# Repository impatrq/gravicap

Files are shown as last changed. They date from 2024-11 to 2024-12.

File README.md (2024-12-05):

<div align="center">

# Proyecto GraviCap

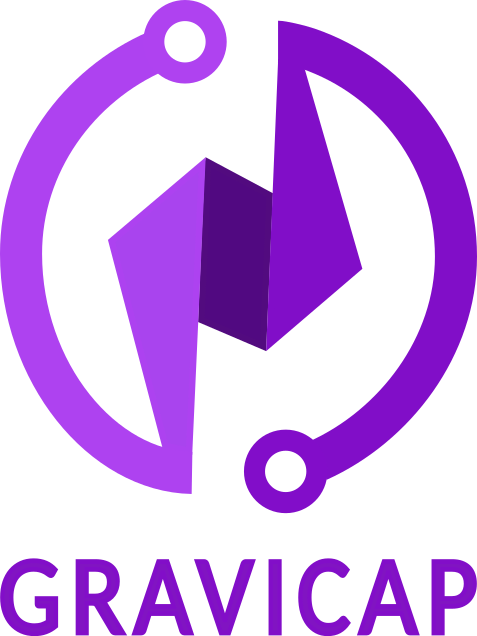
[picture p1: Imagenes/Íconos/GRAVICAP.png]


&nbsp;

| Página web | Email | Instagram | Linktree |
|---|---|---|---|
|[https://gravicap.vercel.app/home](https://gravicap.vercel.app/home)|gravicap.arg@gmail.com|[@gravi.cap](https://www.instagram.com/gravi.cap/)|[https://linktr.ee/gravicap](https://linktr.ee/gravicap)|

&nbsp;

</div>

## ¿Qué es GraviCap?
&nbsp;&nbsp;&nbsp;&nbsp;&nbsp;&nbsp;GraviCap consiste en un condensador de energía gravitatoria junto a un sistema de control de consumo.<br>
&nbsp;&nbsp;&nbsp;&nbsp;&nbsp;&nbsp;Un condensador de energía gravitatoria, o batería de gravedad es una estructura que eleva una carga consumiendo energía eléctrica, para luego almacenarla en forma de energía potencial gravitatoria. El sistema de control de consumo, revisa constantemente elconsumo de energía de la red, eligiendo el momento indicado para soltar la carga, que generará la energía cinética que, luego, será transformada en energía eléctrica por un generador.<br>

## Beneficios
&nbsp;&nbsp;&nbsp;&nbsp;&nbsp;&nbsp;GraviCap es un proyecto ideado para acompañar a los distintos generadores de energías renovables, adaptándose a las dimensiones que desee utilizar su consumidor acorde a la capacidad de su red eléctrica. Procura resguardar su huella de carbono al estar conformado por piezas simples sin requerimientos técnicos en demasía. Gracias a esto, pueden estar fabricadas por materiales reutilizados, derivados de materias primas locales o biomateriales. Permite prescindir aquellos materiales que perjudican al ambiente durante su producción o con su posterior desecho, ya que no hay materiales peligrosos para proteger.<br>
&nbsp;&nbsp;&nbsp;&nbsp;&nbsp;&nbsp;Almacenar energía gravitatoria nos permite ser también sustentables, ya que depende únicamente de un peso y la altura. El almacenamiento de energía es una problemática cada vez mayor, y con un planeta con crecientes problemas ambientales surgen problemas si estos son contaminantes.<br>

## Integrantes:
<div align="center">

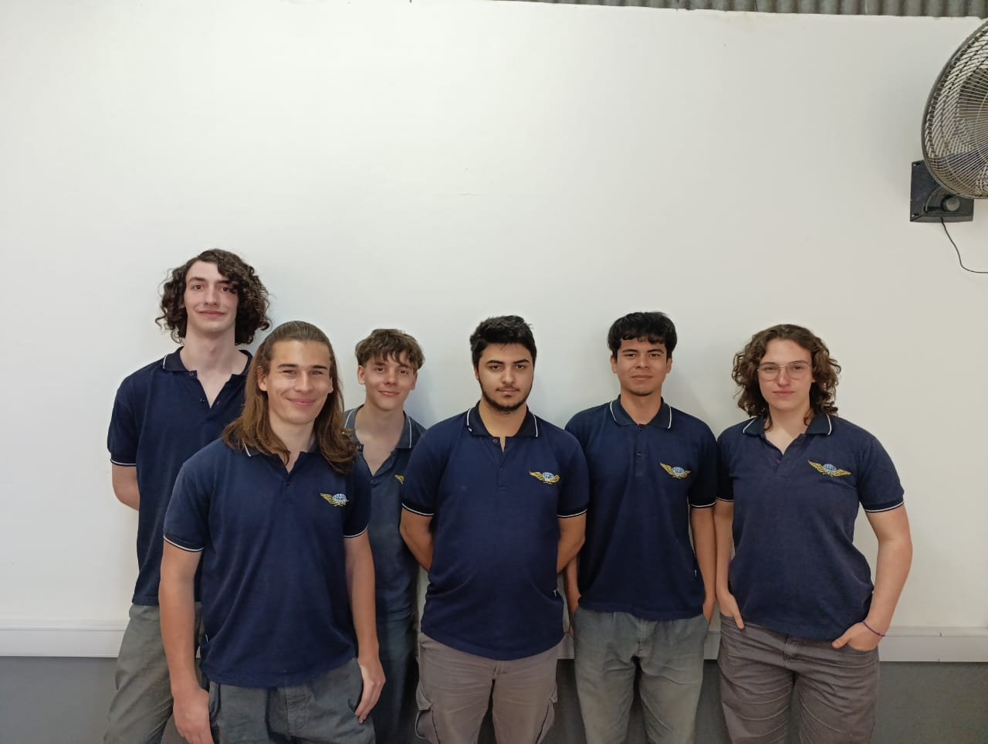
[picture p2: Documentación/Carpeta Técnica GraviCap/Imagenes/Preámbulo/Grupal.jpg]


</div>

### Fausto, Alvarez Mollo
Desarrollo de Electrónica y Documentación.

- 📷 Instagram: @fausto_73

- 📧 faustoalvarezmollo@gmail.com

- LinkedIn: [Fausto Alvarez Mollo](https://www.linkedin.com/in/fausto-alvarez-mollo/)

### Mariano Joaquín Bianqui Kronemberger
Desarrollo Web.

- 📷 Instagram: @marciano_moreno_piripiri

- 📧 marianobianqui@gmail.com

- LinkedIn: [Mariano Joaquín Bianqui Kronemberger](https://www.linkedin.com/in/mariano-bianqui-5035bb303//)

### Tomás Joaquín Calleja
Desarollo de Aplicación.

- 📷 Instagram: @tomii_calleja

- 📧 tomascalleja918@gmail.com

- LinkedIn: [Tomás Joaquín Calleja](https://www.linkedin.com/in/tomás-calleja-5a9894302/)

### Augusto Donatti
Desarrollo Estructural.

- 📷 Instagram: @donatti_augusto0211

- 📧 adonatti2005@gmail.com

- LinkedIn: [Augusto Donatti](https://www.linkedin.com/in/augusto-donatti-54a5bb303/)

### Tatiana Milena Felizia
Desarrollo de Software

- 📷 Instagram: @tati.felizia

- 📧 tatianafelizia@gmail.com

- LinkedIn: [Tatiana Felizia](https://www.linkedin.com/in/tatiana-felizia-9b29141bb/)

### Gabriel Jerónimo Takashi Sofía
Desarrollo de Marketing

- 📧 gabrielsofia19@gmail.com

- LinkedIn: [Gabriel Jerónimo Takashi Sofía](https://www.linkedin.com/in/gabriel-sofia-035335299/)

## Contactanos

### Instagram: [@gravi.cap](https://www.instagram.com/gravi.cap/)

### Pagina web: [gravicap.vercel.app](https://gravicap.vercel.app/home)

### Mail: gravicap.arg@gmail.com

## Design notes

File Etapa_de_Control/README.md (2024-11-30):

# Etapa de Control

&nbsp;&nbsp;&nbsp;&nbsp;&nbsp;&nbsp;La etapa de control es la encargada de sensar en __Tiempo Real__ distintos parámetros asociados al funcionamiento del sistema.
Una vez recolectados, los procesa para controlar el dispositivo y enviarlos a un [servidor web](https://github.com/impatrq/gravicap/tree/main/Servidor_Web).<br>
&nbsp;&nbsp;&nbsp;&nbsp;&nbsp;&nbsp;El sistema es ejecutado por un microcontrolador [RP2040-Zero](https://datasheets.raspberrypi.com/rp2040/rp2040-datasheet.pdf).<br>

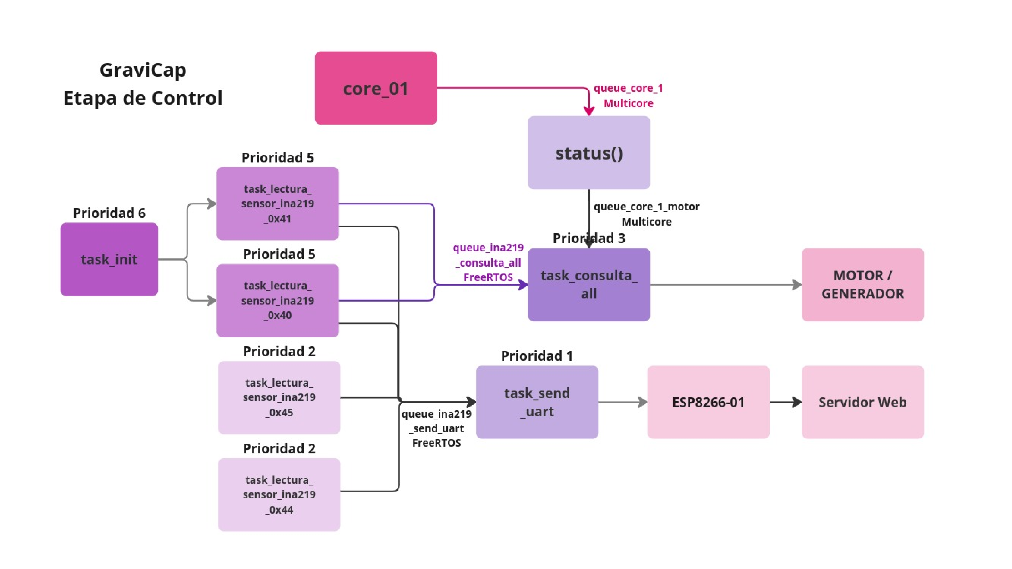
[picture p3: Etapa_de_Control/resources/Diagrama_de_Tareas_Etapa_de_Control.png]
Diagrama de Tareas de FreeRTOS

<div align="center">Diagrama de Tareas de FreeRTOS</div>

## Recursos utilizados
- [FreeRTOS](https://www.freertos.org/)
- [Pico-SDK](https://github.com/raspberrypi/pico-sdk/tree/master)
- [Multicore en RP2040](https://github.com/raspberrypi/pico-sdk/tree/master/src/rp2_common/pico_multicore) 
   
## Componentes utilizados
- [INA219](https://www.ti.com/lit/ds/symlink/ina219.pdf)  
- [Encoder Rotativo Incremental](https://en.wikipedia.org/wiki/Rotary_encoder)
- [ESP8266-01](https://www.espressif.com/sites/default/files/documentation/esp8266-technical_reference_en.pdf)

## Lenguaje utilizado  
&nbsp;&nbsp;&nbsp;&nbsp;&nbsp;&nbsp;C (con soporte de [PlatformIO](https://docs.platformio.org/en/latest/)).
    
## Tipos de comunicación serial  
- __UART__: En el intercambio de información con la [ESP8266-01](https://www.espressif.com/sites/default/files/documentation/esp8266-technical_reference_en.pdf).
- __I2C__: Usado para recibir la entrega de datos de los [INA219](https://www.ti.com/lit/ds/symlink/ina219.pdf), recibe datos en simultáneo desde 4 sensores.

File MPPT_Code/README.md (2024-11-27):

# MPPT - Maximun Power Point Tracking
&nbsp;&nbsp;&nbsp;&nbsp;&nbsp;&nbsp;El MPPT es una técnica utilizada en cargadores para obtener la máxima potencia posible cuando las condiciones de alimentación son inestables en el tiempo.<br>

&nbsp;&nbsp;&nbsp;&nbsp;&nbsp;&nbsp;Esta tecnología es aprovechada por una de las etapas del dispositivo, la que se asegura de convertir de forma óptima la energía entregada por el panel solar 
u otros generadores de energía utilizados. La etapa está conformada por un [circuito electrónico](https://github.com/impatrq/gravicap/tree/main/PCB/MPPT).<br>

&nbsp;&nbsp;&nbsp;&nbsp;&nbsp;&nbsp;El circuito incluye un microcontrolador [RP2040-Zero](https://datasheets.raspberrypi.com/rp2040/rp2040-datasheet.pdf), allí corre el programa presente en este directorio.<br>

## Recursos utilizados
- Lenguaje C (con soporte de [PlatformIO](https://docs.platformio.org/en/latest/))
- Comunicación serial I2C
- Converción Analógico Digital [ADC](https://github.com/raspberrypi/pico-sdk/tree/master/src/rp2_common/hardware_adc)
- [Pico-SDK](https://github.com/raspberrypi/pico-sdk/tree/master)

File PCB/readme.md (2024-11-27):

# PCB
&nbsp;&nbsp;&nbsp;&nbsp;&nbsp;&nbsp;Esta sección contiene todos los diseños de las placas utilizadas por GraviCap<br>

## Contenidos
- PCB Etapa de Control
- PCB MPPT
- PCB Placa de Conexión
  
&nbsp;&nbsp;&nbsp;&nbsp;&nbsp;&nbsp;Además, dentro de cada uno encontrarás:<br>
- Proyecto KiCad
- Archivo PCB
- Archivo SCH

## Recursos Utilizados
- [KiCad](https://www.kicad.org/)

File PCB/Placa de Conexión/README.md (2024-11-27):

Proyecto en KiCad del módulo Step-Down para una conexión a un celular.

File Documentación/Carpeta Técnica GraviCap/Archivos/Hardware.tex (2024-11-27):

\chapter{Hardware}
    
        \section{Introdución}
            El hardware de la Etapa de Control en el sistema \textcolor{dark_violet}{\textbf{GraviCap}} es crucial para la gestión precisa de la energía y el control del movimiento del peso. Esta etapa permite la correcta operación de los motores, sensores y actuadores, asegurando un funcionamiento eficiente del sistema de almacenamiento y conversión de energía. El diseño de este hardware se basa en la implementación de transistores y controladores que trabajan en conjunto para optimizar el flujo de energía y garantizar una operación estable.\par

        \section{Indicadores LED}
            \subsection{Introducción}
                El sistema de control de GraviCap incluye un conjunto de LEDs que proporcionan información visual sobre el estado del sistema y el nivel de carga de la batería. Los LEDs de la derecha indican el estado operativo del sistema, mientras que los LEDs de la izquierda muestran el porcentaje de carga de la batería. Los LEDs están dispuestos para facilitar el monitoreo y permitir una comprensión rápida del estado del sistema.\par
                
            \subsection{LEDs de la Derecha}
                Los LEDs ubicados a la derecha del sistema reflejan el estado general de operación:
                \begin{itemize} [label=•]
                    \setlength{\itemindent}{1.5em}
                    
                    \item Blanco: Indica que el sistema está encendido (ON).
                    \item Azul: Señala que el sistema está en modo de carga, es decir, la batería está recibiendo energía.
                    \item Rojo: Indica que el sistema está en modo de descarga, es decir, la energía almacenada en la batería está siendo utilizada.
                \end{itemize}
                Estos LEDs permiten monitorear el estado activo del sistema de forma clara, mostrando cuándo está operando, cargando o descargando energía.\par
                
            \subsection{LEDs de la Izquierda}
                Los LEDs de la izquierda muestran el porcentaje de carga de la batería, ordenados de arriba hacia abajo según el nivel de carga:\par
                \begin{itemize} [label=•]
                    \setlength{\itemindent}{1.5em}
                    
                    \item Azul: Indica que la batería está al máximo nivel de carga.
                    \item Verde: Señala que la batería está casi completamente cargada.
                    \item Verde (intermedio): Representa que la batería tiene un porcentaje de carga por encima de la mitad.
                    \item Amarillo: Indica que la batería está a la mitad de su capacidad.
                    \item Amarillo (inferior): Indica que la batería está en un nivel de carga inicial.
                    \item Rojo: Señala que la batería está en un estado de carga nulo, es decir, se ha descargado completamente o está cerca de agotarse.
                \end{itemize}
                
                 Este orden secuencial de los LEDs de la izquierda proporciona una visualización rápida del estado de carga de la batería, permitiendo a los usuarios evaluar en qué punto del ciclo de carga o descarga se encuentra la batería con solo un vistazo.\par

        \section{Sistema de Conmutación}
        
            \subsection{Introducción}
                El sistema de conmutación en la Etapa de Control de \textcolor{dark_violet}{\textbf{GraviCap}} se encarga de gestionar el encendido y apagado del motor que controla la masa gravitatoria. Para lograr esto de manera eficiente, se utilizan relés que permiten la conmutación del motor, y estos relés son controlados por transistores BJT. Este sistema garantiza que la conmutación de las corrientes de alto voltaje sea segura y precisa.\par
                
            \subsection{Funcionamiento del Sistema de Conmutación}
                El sistema de conmutación opera mediante un esquema de control en dos etapas. Primero, los transistores BJT actúan como interruptores que controlan la activación de los relés. Estos relés, a su vez, son responsables de conmutar las corrientes de mayor potencia necesarias para el funcionamiento del motor de elevación de la masa.\par
                \begin{itemize} [label=•]
                    \setlength{\itemindent}{1.5em}
                    
                    \item Conmutación con relés: Los relés se utilizan para abrir y cerrar los circuitos de alta corriente que alimentan al motor. Cuando se recibe una señal de control desde el microcontrolador, los BJT se activan, lo que a su vez energiza los relés y permite el paso de corriente hacia el motor.
                    \item Control preciso: El uso de transistores BJT para conmutar los relés permite que el microcontrolador tenga un control preciso sobre cuándo activar o desactivar el motor, asegurando que la operación de carga y descarga se realice en los momentos adecuados.
                \end{itemize}
                
            \subsection{Eficiencia del Sistema de Conmutación}
                El uso de relés para la conmutación del motor, en combinación con los BJT, proporciona un equilibrio entre eficiencia y seguridad. Los relés son ideales para manejar corrientes más altas, mientras que los BJT se encargan de conmutar las señales de control de baja potencia que provienen del microcontrolador.

                \begin{itemize} [label=•]
                    \setlength{\itemindent}{1.5em}
                    
                    \item Relés de alta capacidad: Los relés seleccionados para el sistema pueden manejar las corrientes y voltajes necesarios para operar el motor, asegurando una conmutación confiable sin generar excesivo calor o desgaste en el circuito.
                    \item Conmutación controlada por BJT: Los transistores BJT permiten que la conmutación de los relés sea precisa, ya que estos se activan con señales de baja potencia desde el microcontrolador, lo que garantiza un control eficiente sin necesidad de grandes corrientes para el accionamiento directo de los relés.
                \end{itemize}
                
            \subsection{Protección del Sistema de Conmutación}
                El sistema de conmutación incluye mecanismos de protección que garantizan la seguridad tanto de los relés como de los transistores BJT. Estos mecanismos aseguran que el sistema funcione de manera estable bajo diversas condiciones de carga.\par
                Se han implementado protecciones para evitar que corrientes excesivas dañen los relés o los transistores BJT. Estas protecciones son cruciales para prevenir fallos en el sistema, especialmente durante la conmutación de grandes cargas.\par
            
        \section{Resultado Final}
            \begin{figure}[H]
                    \centering
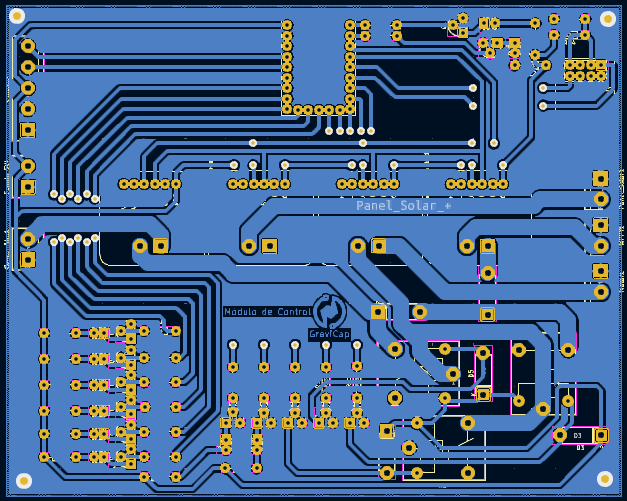
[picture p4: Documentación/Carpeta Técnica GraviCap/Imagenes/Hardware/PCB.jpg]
                    
                    \caption{PCB del Sistema de Control}
                    \label{fig:h1}
                \end{figure}

            \begin{figure}
                \centering
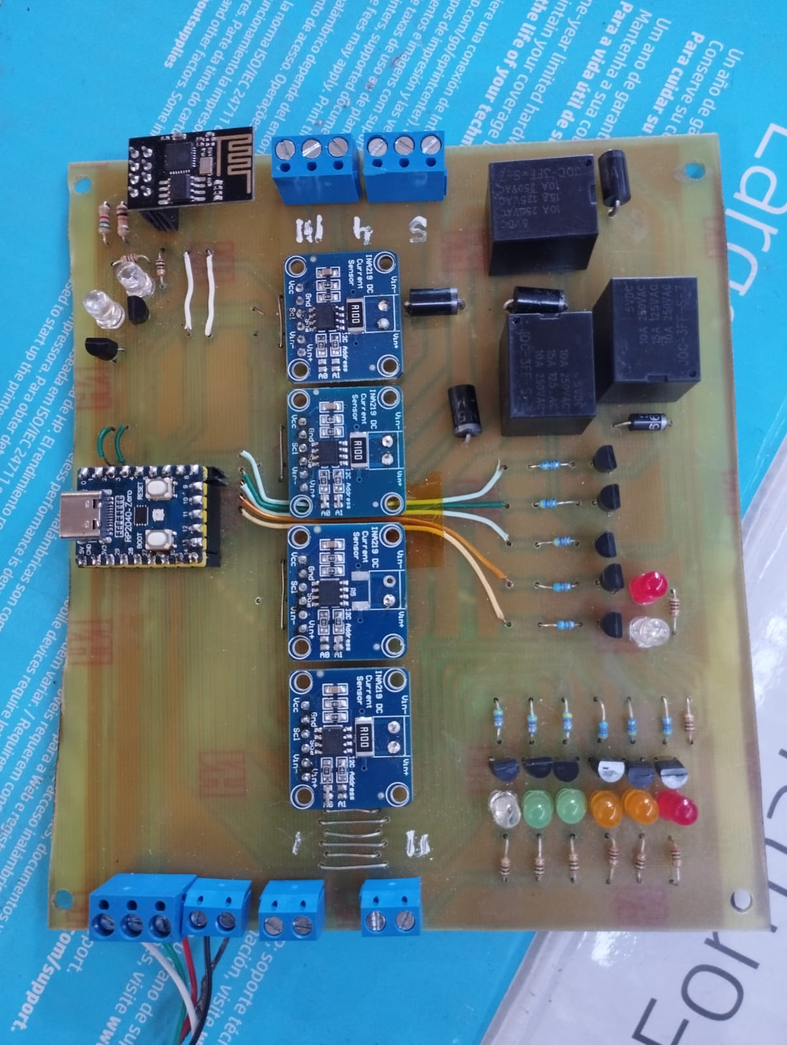
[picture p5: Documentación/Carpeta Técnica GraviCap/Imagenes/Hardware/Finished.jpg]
                
                \caption{PCB finalizado del Sistema de Control}
                \label{fig:h2}
            \end{figure}

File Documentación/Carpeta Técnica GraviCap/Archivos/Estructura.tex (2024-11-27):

\chapter{Estructura}

    \section{Introducción}
    
        Nuestra estructura está diseñada para aprovechar eficientemente la energía potencial gravitatoria mediante un sistema innovador que convierte dicha energía en electricidad utilizable para el consumidor. Este sistema, que se fundamenta en principios físicos sólidos, se basa en la capacidad de almacenar energía cuando se eleva un peso y liberarla controladamente al permitir que dicho peso descienda. Este proceso de elevación y descenso es crucial, ya que permite la conversión de la energía potencial gravitatoria en energía mecánica. A su vez, esta energía mecánica es transformada en energía eléctrica a través de un generador, completando así el ciclo de conversión.\par
        El concepto de energía potencial gravitatoria se basa en la relación entre la masa del objeto, la altura desde la cual se eleva y la fuerza de gravedad que actúa sobre él. Cuando un peso es elevado, se almacena una cantidad significativa de energía, que puede ser aprovechada posteriormente al liberar el peso y dejar que caiga. Este método de almacenamiento y liberación de energía es no solo eficiente, sino también innovador, ya que utiliza la gravedad, una de las fuerzas fundamentales de la naturaleza, como medio para generar electricidad.\par
        El sistema se configura de tal manera que maximiza la conversión de energía y minimiza las pérdidas durante los procesos de elevación y descenso. Al actuar sobre la energía potencial almacenada en el peso, se logra transformar dicha energía en un flujo eléctrico útil que puede ser utilizado para satisfacer las demandas energéticas de los consumidores. Este proceso, que involucra la mecánica del movimiento y la generación eléctrica, es clave para el funcionamiento de la estructura y para alcanzar los objetivos de sostenibilidad y eficiencia energética que perseguimos.\par
        A través de la implementación de este sistema, buscamos demostrar la viabilidad de las baterías gravitatorias como una alternativa renovable y accesible a otras formas de almacenamiento de energía, contribuyendo así a la transición hacia un futuro más sostenible y respetuoso con el medio ambiente.\par
        
    \section{Fundamentos de la Energía Potencial Gravitatoria}
    
        La energía potencial gravitatoria ($E_p$) es la energía que un objeto posee debido a su posición en un campo gravitatorio. En el caso de una batería gravitatoria, el objetivo es aprovechar esta energía elevando una masa a una cierta altura para luego, cuando la masa desciende, convertir esa energía en energía mecánica, y finalmente en energía eléctrica. La fórmula para calcular la energía potencial gravitatoria es:\par
        
        \begin{equation}
            E_p = mgh
        \end{equation}
        
        Donde:\par
        
        \begin{itemize} [label=•]
            \setlength{\itemindent}{1.5em}
            
            \item $E_p$ es la energía potencial en Joules [$J$].
            \item $m$ es la masa del objeto en kilogramos [$kg$].
            \item $g$ es la aceleración de la gravedad ($9,81 \nicefrac{m}{s^2}$).
            \item $h$ es la altura en metros [$m$].
        \end{itemize}
        
        La energía potencial gravitatoria es directamente proporcional a la masa ($m$) y a la altura ($h$). A mayor masa o mayor altura, se almacena más energía. En este sistema, el peso de 27 kg se eleva hasta una altura de 2,2 metros, por lo que la energía potencial almacenada es:\par

        \begin{equation}
            E_p = 27kg \times 9,81 \nicefrac{m}{s^2} \times 2,2m = 582,69 J
        \end{equation}
        
        Esto significa que, cuando el peso está en su posición más alta, el sistema puede almacenar 582.69 Joules de energía, la cual se puede liberar cuando el peso desciende. Si se aumenta la altura o la masa, la energía potencial se incrementará de manera proporcional.\par
        Para un sistema más complejo, donde se utilizan varias masas a distintas alturas, la energía potencial total del sistema sería la suma de las energías potenciales de cada una de esas masas. Esto se expresa como:\par
        
        \begin{equation}
            E_{Total} = \sum_{i=1}^{n} m_igh_i
        \end{equation}

        Dónde:\par

        \begin{itemize} [label=•]
            \setlength{\itemindent}{1.5em}
            
            \item $n$ es el número total de masas.
            \item $m_i$ es la masa de cada bloque.
            \item $h_i$ es la altura de cada bloque.
        \end{itemize}

    \section{Conversión de Energía Potencia a Energía Cinética}

        Cuando la masa desciende desde su posición elevada, la energía potencial gravitatoria ($E_p$) se convierte en energía cinética ($E_k$), que es la energía que un objeto tiene debido a su movimiento. La fórmula para calcular la energía cinética es:

        \begin{equation}
            E_k = \frac{1}{2} m v^2
        \end{equation}

        Dónde:
        \begin{itemize} [label=•]
            \setlength{\itemindent}{1.5em}
            
            \item $E_k$ es la energía cinética generada en Joules [$J$].
            \item $m$ es la masa del objeto en kilogramos [$kg$].
            \item $v$ es la velocidad del objeto en metros sobre segundo [$\nicefrac{m}{s}$].
        \end{itemize}

        Durante el descenso, la masa comienza a ganar velocidad a medida que pierde altura. En un sistema ideal sin pérdidas por fricción o resistencia del aire, la energía cinética adquirida por la masa al llegar al suelo será igual a la energía potencial que tenía en su posición elevada. Es decir, la relación entre la energía potencial y la energía cinética se puede expresar como:\par

        \begin{equation}
            E_p = E_k
        \end{equation}

        Esto significa que toda la energía potencial almacenada cuando la masa estaba en su posición elevada se convierte en energía cinética justo antes de que el peso toque el suelo. A medida que el peso desciende, su velocidad aumenta debido a la aceleración causada por la gravedad ($g$), por lo que la energía cinética aumenta proporcionalmente.\par

        \subsection{Velocidad durante el descenso}
            La velocidad ($v$) de la masa al caer desde una altura $h$ se puede calcular usando la siguiente fórmula derivada de las leyes de la conservación de la energía:\par

            \begin{equation}
                v = \sqrt{2gh}
            \end{equation}

            Dónde:\par

            \begin{itemize} [label=•]
                \setlength{\itemindent}{1.5em}
                
                \item $v$ es la velocidad en metros sobre segundos [$\nicefrac{m}{s}$].
                \item $g$ es la aceleración de la gravedad ($9,81 \nicefrac{m}{s^2}$).
                \item $h$ es la altura desde la que cae la masa en metros [$m$].
            \end{itemize}

            En nuestro sistema, con una altura de 2,2, la velocidad al llegar al punto más bajo será:\par

            \begin{equation}
                v = \sqrt{2 \times 9,81 \nicefrac{m}{s^2} \times 2,2m} = 6,57 \nicefrac{m}{s}
            \end{equation}

            Este valor indica que la masa de 27 kg alcanzará una velocidad de 6,57 $\nicefrac{m}{s}$ cuando caiga desde su altura máxima de 2,2 metros. Esta velocidad genera la energía cinética que es clave para la conversión de energía en el generador.\par
        
    \section{El Motor/Generador y el Sistema de Poleas}
        
        El motor/generador es el corazón de la conversión de energía. Este dispositivo no solo convierte la energía mecánica en electricidad, sino que también es responsable de elevar la masa para almacenar energía.\par
        El torque ($\tau$) es fundamental para el funcionamiento del sistema, ya que determina cuánta fuerza puede aplicar el motor para mover la masa. La relación entre el torque y la velocidad angular ($\omega$) se utiliza para calcular la potencia generada por el motor:\par

        \begin{equation}
            P = \tau\omega
        \end{equation}

        Dónde:\par

        \begin{itemize} [label=•]
            \setlength{\itemindent}{1.5em}
            
            \item $P$ es la potencia en Watts ($W$),
            \item $\tau$ es el torque en Newton-metros ($Nm$),
            \item $\omega$ es la velocidad angular en radianes por segundo ($rad/s$).
        \end{itemize}

        Para convertir las 11 RPM a radianes por segundo:\par

        \begin{equation*}
            \omega = \frac{11RPM \times 2\pi}{60} = 1,15 \nicefrac{rad}{s}
        \end{equation*}

        Ahora, usando la potencia del motor (195W):\par

        \begin{equation}
            \tau = \frac{195W}{1,15 \nicefrac{rad}{s}} = 169,57 Nm
        \end{equation}

        Este cálculo es esencial para determinar cuánta energía mecánica se convierte en energía eléctrica. En este sistema, las poleas juegan un papel crucial al facilitar el movimiento del peso, reduciendo la fuerza necesaria para levantar la masa y optimizando el uso de energía. El sistema de poleas también asegura que el peso descienda de manera controlada, lo que permite una conversión eficiente de la energía mecánica en electricidad.\par

        \subsection{Tiempo de Carga y Descarga}
            El tiempo de carga en una batería gravitatoria se refiere al tiempo necesario para elevar el peso hasta su posición más alta, donde la energía potencial se almacena. Este proceso depende de la velocidad a la que el motor/generador puede elevar el peso y de la cantidad de energía disponible para realizar esta tarea. Por otro lado, el tiempo de descarga está relacionado con el tiempo que toma para que el peso descienda controladamente, convirtiendo la energía potencial en energía cinética, y finalmente, en energía eléctrica.\par

            \subsubsection{Tiempo de Carga}
                El tiempo de carga está influenciado por la potencia del motor que eleva el peso. Si se conoce la potencia del motor y la energía que se necesita para elevar el peso a una cierta altura, se puede calcular el tiempo de carga utilizando la relación entre trabajo, potencia, y tiempo:\par

                \begin{equation}
                    P = \frac{W}{t} \Rightarrow t = \frac{W}{P}
                \end{equation}

                Dónde:\par
                
                \begin{itemize} [label=•]
                    \setlength{\itemindent}{1.5em}
                    
                    \item $P$ es la potencia generda por el motor en Watts [$W$].
                    \item $W$ es el trabajo realizado para elevar el peso, que en este caso es igual a la energía potencial gravitatoria ($E_p$) en Joules [$J$].
                    \item $t$ es el tiempo de carga en segundos [$s$].
                \end{itemize}

            \subsubsection{Tiempo de Descarga}
                El tiempo de descarga está relacionado con la velocidad de descenso del peso, que se controla mediante el generador. El generador actúa como un freno controlado, permitiendo que el peso descienda a una velocidad óptima para maximizar la conversión de energía cinética en energía eléctrica. El tiempo de descarga puede ser más largo o más corto dependiendo de cuánta energía se necesita en un momento dado y cómo se gestiona el proceso de conversión.\par
                El tiempo de descarga está directamente vinculado a la velocidad de caída del peso, que a su vez depende de la aceleración debida a la gravedad y de la resistencia del sistema de frenado. Si el sistema permite un descenso rápido, la energía se liberará en un corto período de tiempo, pero podría no ser eficiente si no se sincroniza bien con las demandas energéticas. Si el sistema permite un descenso más lento y controlado, la descarga puede durar más tiempo, suministrando energía de manera continua y estable.\par
                Para estimar el tiempo de descarga, se puede controlar la velocidad angular del generador, ajustando el freno para que la masa descienda a una velocidad que maximice la eficiencia de conversión. Esta velocidad dependerá de las características del generador y de las necesidades de la red o del sistema que está consumiendo la energía.\par

        \subsection{Potencia entregada durante la Descarga}
            Durante la descarga, el motor actúa como generador, y la potencia entregada durante este proceso depende de la energía cinética generada por el descenso del peso. La potencia generada ($P_{Generada}$) puede calcularse con la siguiente fórmula:\par

            \begin{equation}
                P_{Generada} = \frac{E_k}{t}
            \end{equation}

            Dónde:\par
            
            \begin{itemize} [label=•]
                \setlength{\itemindent}{1.5em}
                
                \item $E_k$ es la energía cinética en Joules [$J$].
                \item $t$ es el tiempo de descarga [$s$].
            \end{itemize}

            Si durante el descenso el peso genera una energía cinética de 582.69 Joules (que es el valor de la energía potencial almacenada), y el tiempo de descarga es 6 segundos, la potencia generada sería:\par

            \begin{equation}
                P_{Generada} = \frac{582,69 J}{6 s} = 97,115 W
            \end{equation}
            
        \section{Conversión de Energía y Rendimiento del Sistema}
    
        El rendimiento del sistema está influenciado por la eficiencia del motor/generador y por las pérdidas de energía en los procesos de conversión. Es fundamental diseñar el sistema de manera que las pérdidas, ya sea por fricción o por resistencias eléctricas, sean mínimas para maximizar la cantidad de energía útil que se puede obtener del sistema.\par
        El rendimiento ($\eta$) de un motor o generador se define como la relación entre la potencia útil ($P_u$) y la potencia absorbida ($P_a$):\par

        \begin{equation}
            \eta = \frac{P_u}{P_a} \times 100\%
        \end{equation}
        
        Las pérdidas pueden surgir por diversas razones, tales como:\par

        \begin{itemize} [label=•]
            \setlength{\itemindent}{1.5em}
            
            \item Fricción en los componentes mecánicos, como las poleas y rodamientos.
            \item Pérdidas resistivas en el sistema eléctrico, que se producen cuando la corriente fluye a través de cables y conexiones que presentan resistencia.
            \item Calor generado por el motor durante su funcionamiento, que puede resultar en una disminución de la eficiencia si no se gestiona adecuadamente.
        \end{itemize}
        
        \section{Estructura y Diseño}
        
        La estructura, de 2,2 metros de altura y 27 kg de peso, está diseñada para soportar la masa que se eleva. El diseño debe garantizar la estabilidad y la seguridad del sistema, especialmente en la parte superior donde se monta el motor/generador. La resistencia de la estructura se puede calcular usando la fuerza ejercida sobre ella, que es el peso de la masa multiplicado por la gravedad:\par

        \begin{equation*}
            F = mg
        \end{equation*}

        Entonces:\par

        \begin{equation}
            F = 27kg \times 9,81 \nicefrac{m}{s^2} = 264,87N
        \end{equation}

        Esta fuerza de 264,87 Newtons es la carga que la estructura debe soportar de manera constante. En el diseño estructural, es necesario asegurarse de que los materiales seleccionados puedan soportar esta carga sin deformarse ni fallar. La resistencia del material, $\sigma$, puede calcularse si se conoce el área de la sección transversal del material ($A$):\par

        \begin{equation}
            \sigma = \frac{F}{A}
        \end{equation}

        Para mantener la integridad del sistema, el diseño de la base y las conexiones entre los diferentes componentes deben distribuir esta fuerza de manera uniforme.\par

        \subsection{Ejecución}
            En el marco de nuestro proyecto académico, hemos desarrollado un prototipo a escala para demostrar la viabilidad de las baterías de gravedad como un sistema de almacenamiento de energía sostenible. Si bien este prototipo no representa el tamaño completo de una instalación comercial, cumple la función de ilustrar los principios físicos fundamentales y demostrar cómo se puede aplicar la tecnología de almacenamiento energético basada en la energía potencial gravitatoria.\par

            \begin{figure}[H]
                \centering
                \begin{subfigure}[b]{0.3\textwidth}
                    \centering
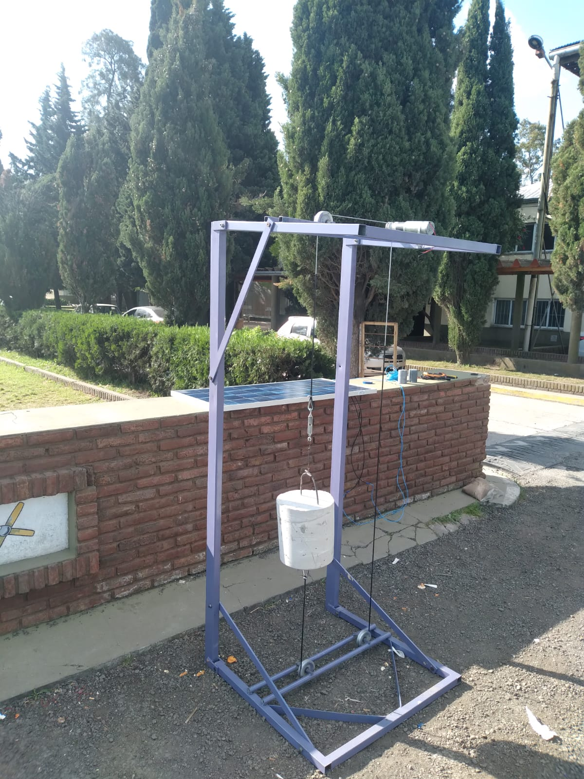
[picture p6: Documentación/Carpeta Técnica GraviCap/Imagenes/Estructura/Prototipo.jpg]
                    
                    \caption{Prototipo de \textcolor{dark_violet}{\textbf{GraviCap}}}
                    \label{fig:e1.1}
                \end{subfigure}
                \begin{subfigure}[b]{0.3\textwidth}
                    \centering
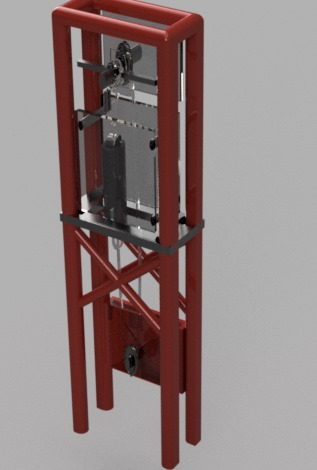
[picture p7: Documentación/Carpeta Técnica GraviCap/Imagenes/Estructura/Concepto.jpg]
                    
                    \caption{Concepto de \textcolor{dark_violet}{\textbf{GraviCap}}}
                    \label{fig:e1.2}
                \end{subfigure}
                \caption{\textcolor{dark_violet}{\textbf{GraviCap}}}
                \label{fig:e1}
            \end{figure}
            
            Como alumnos, este proyecto es también una parte crucial de nuestro aprendizaje. Nos brinda la oportunidad de aplicar los conocimientos adquiridos en física, mecánica y sistemas eléctricos, además de desarrollar habilidades prácticas de diseño, ejecución y resolución de problemas. El prototipo a escala ha sido un paso esencial para comprender las implicaciones reales de implementar una batería gravitatoria, permitiéndonos abordar desafíos técnicos que probablemente también enfrentaríamos en una versión a mayor escala.\par
            El desarrollo de este prototipo nos ha proporcionado una visión clara de los beneficios y limitaciones de las baterías de gravedad, así como una base para futuras investigaciones y mejoras tecnológicas. Si bien nuestro prototipo no tiene la capacidad de almacenar grandes cantidades de energía, demuestra que esta tecnología es factible y escalable.\par
            Este enfoque educativo también nos motiva a pensar en soluciones reales para problemas energéticos actuales, como la necesidad de almacenamiento de energía renovable a gran escala, lo que refuerza la relevancia de nuestro trabajo en el contexto global de sostenibilidad y energía limpia.\par

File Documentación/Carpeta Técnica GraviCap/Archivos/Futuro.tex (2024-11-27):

\chapter{Limitaciones y Próximos Pasos}

    \section{Limitaciones}
        Durante el desarrollo del proyecto \textcolor{dark_violet}{GraviCap}, nos enfrentamos a varias limitaciones propias de trabajar con recursos restringidos y bajo las condiciones de un grupo de estudiantes en una escuela secundaria técnica. Estas limitaciones afectaron tanto el diseño como la implementación del prototipo, pero también nos ofrecieron valiosas lecciones sobre cómo escalar y mejorar el sistema en el futuro.\par
        
        \subsection{Capacidad de Almacenamiento de Energía}
        
            Una de las principales limitaciones del prototipo es la capacidad de almacenamiento de energía, que está determinada principalmente por la masa utilizada y la altura a la que puede ser elevada. El sistema actual utiliza una masa de 27 kg y una altura de 2,2 metros, lo que permite almacenar una cantidad limitada de energía potencial gravitatoria. Aunque esto es suficiente para demostrar el principio de funcionamiento del sistema, resulta insuficiente para aplicaciones a gran escala. La fórmula de la energía potencial, $E_p = mgh$, muestra que, para aumentar la capacidad de almacenamiento, sería necesario elevar la masa a mayores alturas o utilizar cargas más pesadas, lo que presenta desafíos adicionales en términos de infraestructura y control.\par
            
        \subsection{Eficiencia del Motor/Generador}
        
            Otro desafío importante fue la eficiencia del motor/generador. El prototipo utiliza un motor con una potencia de 195W y una reducción significativa de la velocidad, de 8100 RPM a 11 RPM. Aunque este sistema ha demostrado ser funcional para el prototipo, las pérdidas de energía durante la conversión de energía potencial en energía eléctrica siguen siendo un problema. Los motores utilizados para la generación de energía en aplicaciones industriales suelen tener una mayor eficiencia, lo que sugiere que, para futuras versiones del proyecto, sería necesario invertir en motores de mejor calidad y reducir las fricciones mecánicas en el sistema.\par
            
        \subsection{Infraestructura Limitada}
            El espacio disponible y los materiales utilizados también representaron una limitación. Nuestro prototipo fue diseñado y construido con materiales reciclados y reutilizados, lo cual tiene un impacto positivo en el costo y la sostenibilidad del proyecto. Sin embargo, para un sistema comercialmente viable, la infraestructura debe ser más robusta y estar diseñada específicamente para soportar grandes cargas durante largos períodos de tiempo sin riesgo de deterioro estructural.\par
    
    \section{Próximos Pasos}
    
        A pesar de las limitaciones mencionadas, el proyecto \textcolor{dark_violet}{GraviCap} tiene un enorme potencial para ser escalado y mejorado, no solo a nivel técnico, sino también en cuanto a su impacto en el almacenamiento de energía renovable. Basándonos en lo aprendido durante el desarrollo del prototipo, los próximos pasos a seguir incluirán tanto mejoras en el diseño del sistema como la implementación de nuevas tecnologías para aumentar su eficiencia y capacidad.\par
        
        \subsection{Escalado del Sistema}
        
            El paso más inmediato es aumentar la escala del sistema. Esto implicará la construcción de una versión más grande del prototipo, utilizando masas más pesadas y elevándolas a mayores alturas para incrementar la capacidad de almacenamiento de energía. Además, se considerarán nuevas configuraciones que permitan optimizar el uso del espacio y mejorar la conversión de energía potencial en electricidad.\par
            
        \subsection{Optimización del Motor/Generador}
        
            Se buscarán motores y generadores más eficientes para maximizar la cantidad de energía que se puede recuperar durante el proceso de descarga. Esto podría incluir la implementación de motores de última generación, con menores pérdidas por fricción y una mayor capacidad de conversión de energía mecánica en eléctrica. También se evaluarán nuevas configuraciones de poleas y sistemas de transmisión para reducir las pérdidas mecánicas en el sistema.\par
        
        \subsection{Ampliación de Aplicaciones}
        
            Un aspecto clave del futuro de \textcolor{dark_violet}{GraviCap} será su adaptabilidad a diferentes escenarios de uso. Aunque el prototipo actual ha sido desarrollado principalmente como una demostración a pequeña escala, el sistema podría adaptarse a necesidades específicas, como el almacenamiento de energía en zonas rurales sin acceso a la red eléctrica o como respaldo energético para sistemas solares. A medida que el proyecto crezca, se buscará que la tecnología sea accesible y económicamente viable para su implementación a distintas escalas.\par
        
        \subsection{Pruebas y Validación}
            Finalmente, es esencial que el sistema sea sometido a pruebas rigurosas en condiciones reales. Se planifican pruebas adicionales para evaluar el rendimiento del sistema en diferentes entornos, considerando factores como la temperatura, la humedad y las condiciones de carga variables. Estas pruebas ayudarán a identificar cualquier posible fallo y permitirán ajustar el diseño antes de implementar el sistema a mayor escala.\par

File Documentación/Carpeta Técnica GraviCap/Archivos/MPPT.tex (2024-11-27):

\chapter{Cargador MPPT}
    
        \section{¿Qué es MPPT?}
        
            \textit{Maximum Power Point Tracking} es una técnica utilizada en cargadores para obtener la máxima potencia posible cuando las condiciones de alimentación son inestables.\par
            En los sistemas que utilizan, por ejemplo, energía solar la energía entregada depende de factores como la cantidad de luz, sombra, temperatura de los paneles, entre otras cosas. Cuando las condiciones son inestables, la impedancia característica que establece el punto de transferencia de potencia varía. Así, el sistema es optimizado cuando las condicones de la carga varían. A esto se le llama \textbf{MPP} (\textit{Maximum Power Point}) y al proceso \textbf{MPPT}\par
            
        \section{Principio de funcionamiento}
        
            \subsection{Convertidor DC-DC}
                Para convertir de un voltaje de continua de entrada mayor a uno menor, existen una infinidad de opciones. Se podría realizar un divisor resistivo, el cual disipa la potencia que no querramos, que sería poco eficiente. Para ocaciones en las que se busca conservar la máxima eficiencia posible con la mínima pérdida de potencia posible.\par
                Ahí es dónde entra el conversor Buck, o conversor reductor, que a la vez que reduce el voltaje de salida aumenta la corriente de salida, manteniendo constante la potencia. Es una clase de fuente switching, y provee una eficiencia muy alta, por encima de un 90\%. Además, controlando la señal de switching, podemos variar el voltaje de salida a voluntad.\par

                \begin{figure}[!ht]
                    \centering
                    \begin{subfigure}[b]{0.3\textwidth}
                        \centering
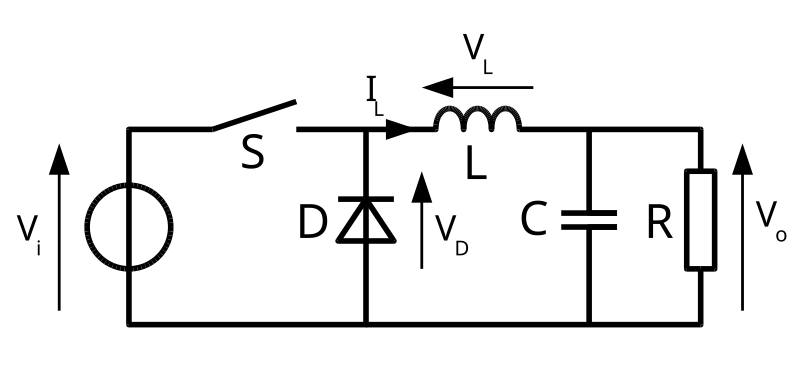
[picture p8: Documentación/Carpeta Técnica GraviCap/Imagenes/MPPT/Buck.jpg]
                        
                        \caption{Componentes del Conversor Buck}
                        \label{fig:m1.1}
                    \end{subfigure}
                    \begin{subfigure}[b]{0.3\textwidth}
                        \centering
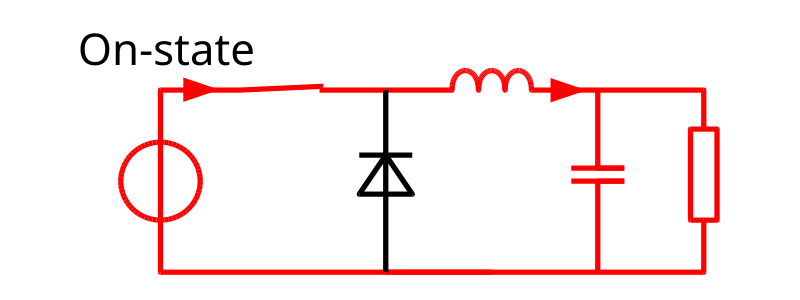
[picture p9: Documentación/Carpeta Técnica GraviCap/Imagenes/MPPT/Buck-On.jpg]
                        
                        \caption{Estado On del Conversor Buck}
                        \label{fig:m1.2}
                    \end{subfigure}
                    \begin{subfigure}[b]{0.3\textwidth}
                        \centering
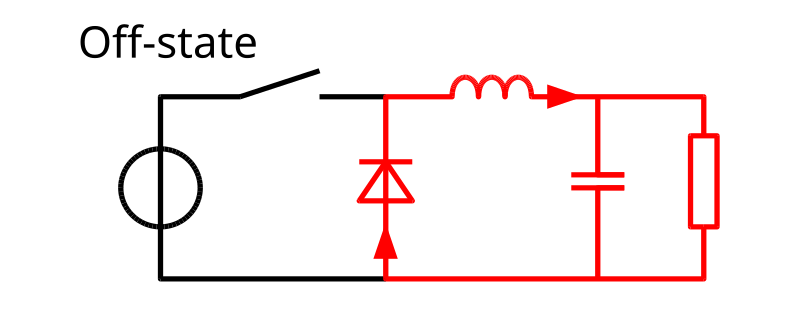
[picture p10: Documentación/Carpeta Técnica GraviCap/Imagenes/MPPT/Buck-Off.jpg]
                        
                        \caption{Estado Off del conversor Buck.}
                        \label{fig:m1.3}
                    \end{subfigure}
                    \caption{Conversor Buck}
                    \label{fig:m1}
                \end{figure}

                Para entender este circuito, se debe hacer un análisis del estado transitorio del mismo en sus dos estados, On y Off. En principio, con el estado Off, la corriente en el circuito es nula. Cuando cambia al estado On, la corriente va empezar a subir y la bobina va a generar una caída de voltaje entre sus terminales. Esta caída de voltaje provoca que el voltaje resultante en la carga sea menor. A medida que pasa el tiempo, el índice de cambio de la corriente disminuye, y el voltaje en la bobina también disminuye, aumentando el voltaje en la carga. Durante este proceso, la bobina almacena energía en forma de campo magnético\par
                Cuando el interruptor de abre de vuelta (Off), la fuente de voltaje se remueve del circuito y la corriente disminuye. Esta corriente decreciente produce una caída de voltaje en la bobina (opuesto al generado en el estado On), y ahora la bobina se convierte en una fuente de corriente. La energía almacenada en el campo magnético de la bobina suporta el flujo de corriente por la carga. Esta corriente, que fluye mientras la fuente de voltaje está desconectada, cuando se suma a la corriente que fluye en el estado On, da como resultado una corriente de salida promedio mas grande que la que entrega la fuente de voltaje.\par

                \begin{figure} [!ht]
                    \centering
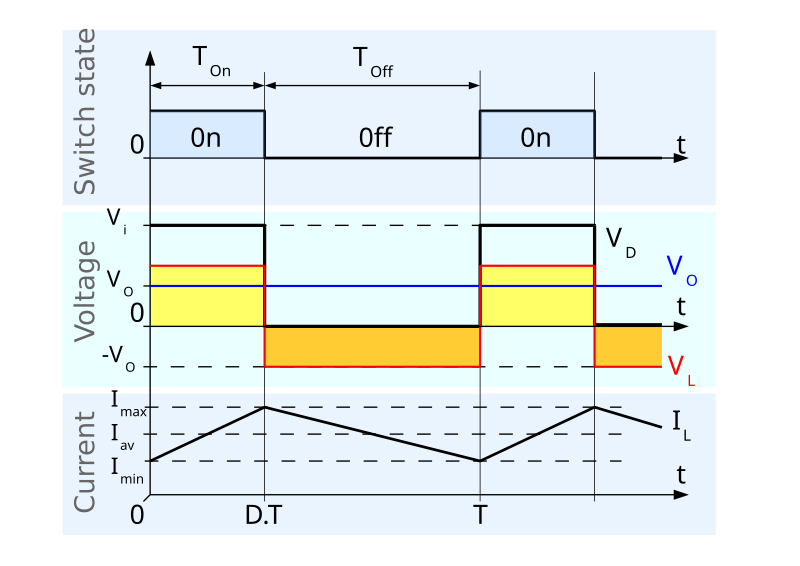
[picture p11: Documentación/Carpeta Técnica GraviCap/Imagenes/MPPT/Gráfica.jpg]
                    
                    \caption{Gráfica en el tiempo del comportamiento de las tensiones y corrientes de un convertidor buck.}
                    \label{fig:m1.4}
                \end{figure}
                
                Este aumento en la corriente promedio estaría compensando la reducción en el voltaje, manteniendo idealmente la potencia entregada en la carga. Si el switch se abre mientras la corriente sigue aumentando, entonces siempre va a haber una caída de tensión sobre la bobina, por lo tanto la carga siempre tendra menos voltaje que la entrada.\par

            \subsection{Sistema de Control}
                Si uno logra variar la frecuencia con la que ese switch se abre y se cierra, y al mismo tiempo medir la corriente y la tension recibida en la carga, se puede diseñar un sistema de control que, teniendo en cuenta esas variables, varíe esa frecuencia del interruptor con esas mediciones como realimentación, controlando una o la otra.\par
                El sistema de control que utilizamos es un control proporcional integral, o \textbf{PI}, siendo la aplicación de un control proporcional y uno integral al mismo tiempo.\par
                La parte proporcional de un control es el producto entre la señal de error ($e_{(t)}$) y la constante proporcional ($K_p$). Variando ($K_p$) se cambia la velocidad del control. Pero solo con un control proporcional se tiene error en régimen permanente, ya que este tipo de control requiere de error para entregar señal de control. La fórmula matemática que responde a esto es:\par
                \begin{equation}
                    P_{sal} = K_p \times e_{(t)}
                \end{equation}
                La parte integral del control actua cuando hay una desviación entre la variable y el punto de consigna, integrando esta desviación en el tiempo. El error es integrado, lo cual tiene la función de promediarlo o sumarlo por un período determinado, y luego se multiplica por una constante $K_i$. Elimina el error de estado estacionario, logrando seguimiento perfecto de la señal de referencia. La fórmula matemática que responde a esto es:\par
                \begin{equation}
                    I_{sal} = K_i \times \int e_{(t)} \ dt
                \end{equation}
                
        \section{Realización}
            \subsection{Esquemático}
                Se podrá encontrar el esquemático en el Apéndice A, que contiene los esquemáticos del proyecto.\par
            
            \subsection{Hardware}
                Para la realización de este cargador utilizamos una \textbf{RP2040 Zero}. Que luego se comunicará con el módulo de control para informar sobre los parámetros medidos.\par
                Para la medición de la corriente utilizamos un módulo \textbf{INA 219} que nos permite medir de forma precisa los parámetros de corriente.\par
                Para medir las tensiones tanto de entrada como de salida simplemente utilizamos divisores resistivos, los cuales nos devuelven voltajes proporcionales reducidos, tambien procesados por los otros dos ADCs de la RP2040 Zero. Para la conversion simplemente se tiene en cuenta la relacion de las resistencias.\par
                Para la alimentación del circuito se aprovecha el voltaje entregado por el cargador, donde conectamos una fuente stepdown que regula la tensión entregada por el cargador a 5V para la alimentación de la RP2040 Zero. Esto quiere decir que una vez que se conecta, el circuito ya se encuentra alimentado por energías renovables.\par
                En el circuito MPPT, la única diferencia con el teórico es el interruptor. Nuestro interruptor es un MOSFET canal P IRF4905, que resiste hasta 70A de corriente. Es necesaria la utilización de un MOSFET canal P porque la carga del mismo tiene que estar entre Drain y Masa, mientras que la carga de un canal N tiene que estar entre la alimentación y Source, algo que en nuestro diseño resultó inconveniente.\par
                Para conmutar este MOSFET con la RP2040, no solo fue necesaria la utilización de un transistor NPN, sino tambien la de un circuito totem pole\par
                Un circuito totem pole consta de 2 transistores, un PNP y un NPN, uno arriba del otro, con sus bases interconectadas. Esto nos permite conmutar el MOSFET sin problemas, porque admite corrientes en ambos sentidos, tanto positivas como negativas. Esto es necesario porque un MOSFET necesita ambos sentidos de corrientes. Para entrar en estado de corte, necesita una corriente positiva en el Gate, y para volver al estado de saturación, por las características capacitivas del mismo, genera una corriente negativa.\par
                Para el cálculo del inductor, se realizó el siguiente procedimiento:\par
                Fijándose en la figura \ref{fig:m1.4}, el aumento de la corriente en la bobina queda:\par
                \begin{equation}
                    \frac{di_L(t)}{dt} = \frac{V_L(t)}{L} = \frac{V_i - V_o}{L}
                \end{equation}
                y análogamente el descenso de la corriente es:\par
                \begin{equation}
                    \frac{di_L(t)}{dt} = \frac{V_L(t)}{L} = \frac{-V_o}{L}
                \end{equation}
                Como toda la energía que se almacena en la bobina durante el primer estado se transfiere durante el segundo, la energía del inductor al final del periodo de conmutación ($T_S$) es igual en $t = 0$ y en $t = T_S$.\par
                Por lo tanto, la tensión media en la bobina ⟨$V_L$⟩ en régimen permanente es nula, es decir, existe una igualdad en las áreas.\par
                \begin{equation}
                    \langle V_L \rangle = \frac{1}{T_S}\int_{T_S} V_L dt = 0
                \end{equation}
                Aplicando la ecuación se obtiene:\par
                \begin{equation}
                    (V_i - V_o) \cdot DT_S - V_o \cdot (T_S - DT_S) = 0
                \end{equation}
                Donde $D$ es un número adimensional, entre 0 y 1, denominado ciclo de trabajo. Siendo que este no puede ser mayor a 1, se cumple $V_o \leq V_i$, por tanto solo se podrá reducir la tensión.\par
                \begin{equation}
                    V_o = D \cdot V_i
                    \label{eq:D}
                \end{equation}
                La corriente media que circula por la bobina, con un D del 10\% (peor condición posible):\par
                \begin{equation}
                    I_L > \frac{I_{Lmax}}{10} = 1A
                \end{equation}
                
                \begin{equation}
                    \frac{\Delta I_L}{2} < 1A \Rightarrow \Delta I_L < 2A
                \end{equation}\\
                Para calcular la bobina, se utiliza la siguiente fórmula:\par
                \begin{equation}
                    \frac{V_i - V_o}{L} \cdot D \cdot T_S < 2A
                \end{equation}\\
                Reemplazando D por la equivalencia obtenida en la fórmula \ref{eq:D}, queda:\par
                \begin{equation}
                    L \geq \frac{V_o(1-\frac{V_o}{V_i})\cdot T_S}{2}
                \end{equation}
                Siendo\par
                    \[V_i [24V-48V]\]
                    \[V_o [24V-28V]\]
                    \[T_S = 32 \cdot 10^{-6} S  = 32KHz\]\\
                El máximo de esta función queda definido por los máximos valores de tensión de entrada y tensión de salida, por lo tanto:\par
                \begin{equation}
                    L \geq \frac{28 \cdot (1-\frac{28}{48}) \cdot 32 \cdot 10^{-6}}{2}
                \end{equation}
                Entonces \[L \geq 99,5\mu H\]\\
                La bobina utilizada en el circuito posee un valor de \textbf{$83 \mu H$}, la cual cumple con la condición anterior.\\
                Para el cálculo del capacitor correspondiente, se realizó el siguiente procedimiento:\\
                Cálculo para el ripple del capacitor de un 1\%:\par
                \begin{equation}
                    \Delta V_o = 1\% \cdot 28V = 0,28V
                \end{equation}
                La fórmula utilizada para obtener el valor del capacitor es la siguiente:\\
                \begin{equation}
                    \Delta V_o = \frac{V_o \cdot (1-\frac{V_o}{V_i})}{8 \cdot L \cdot C \cdot F^2}
                \end{equation}\\
                Despejando, se obtiene:\\
                \begin{equation}
                    C \geq \frac{V_o \cdot  (1 - \frac{V_o}{V_i})}{8 \cdot L \cdot \Delta V_o \cdot F^2}
                \end{equation}\\
                Con los valores ya calculados, se reemplazan los parámetros:\\
                \begin{equation}
                    C \geq \frac{28V \cdot (1 - \frac{28V}{36V})}{8 \cdot 83 \mu H \cdot 32KHz^2}
                \end{equation}
                Entonces \[C \geq 27,13 \mu F\]\\
                Para evitar resonancias, se estima que la frecuencia de resonancia tiene que estar 10 veces por debajo de la frecuencia en la que se trabaja. Por esto:\\
                \begin{equation}
                    \frac{F_S}{10} = \frac{1}{\sqrt{L \cdot C}}
                \end{equation}
                Despejando, queda:\\
                \begin{equation}
                    C = \frac{10^2}{32KHz^2 \cdot 27,13 \mu H} \simeq 2713 \mu F
                \end{equation}\\
                Por lo tanto, en el circuito final se utilizó un capacitor de \textbf{$3300 \mu F$}

            \subsection{Software}
                El sistema MPPT fue programado íntegramente con el lenguaje C sobre la RP2040.\par
                El microcontrolador lee las señales del divisor de tensión que caerá sobre sus ADC y, mediante una lógica dependiente de la relación entre las resistencias del divisor de tensión, el código interpreta estas señales para saber el valor deseado (ya sea corriente o votaje).\par
                Ya sabiendo los valores que se tienen que medir, se compararán con los valores definidos para el cambio de lógica. Así se define en que modo de carga estará el MPPT. Por ejemplo, para el cambio entre BULK y ABSORTION, el voltaje de la batería deberá ser mayor al voltaje máximo definido del modo BULK.\par
                Cada modo tiene su propia lógica para manejar el PWM que regula la tensión y corriente que le llega a la batería. En el modo BULK, primero se calcula el error entre la medicion actual y la deseada, luego se ve si la corriente que le llega a la batería es mayor o menor a la deseada y en base a esto se controla el PWM proporcionalmente e integralmente tomando en cuenta el error, pasando previamente por un saturador, asegurándose que el valor del PWM no sea ni mayor a 100\% ni menor a 0\%.\par
                Para conocer más sobre todo esto, referirse al Anexo B, más específicamente el Listing B.1.
                
            \section{Resultado Final}
                \begin{figure}[H]
                    \centering
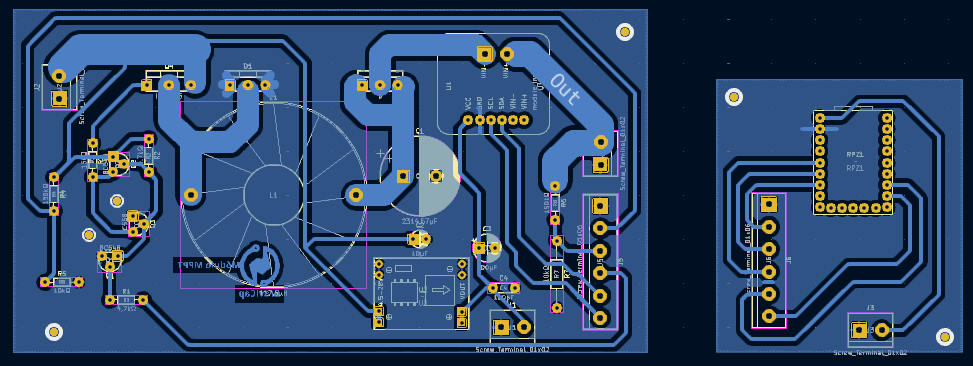
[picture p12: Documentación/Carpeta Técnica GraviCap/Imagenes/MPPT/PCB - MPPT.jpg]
                    
                    \caption{PCB del MPPT}
                    \label{fig:m5.1}
                \end{figure}

                \begin{figure}
                    \centering
                    
                    \caption{PCB finalizado del MPPT}
                    \label{fig:m5.2}
                \end{figure}

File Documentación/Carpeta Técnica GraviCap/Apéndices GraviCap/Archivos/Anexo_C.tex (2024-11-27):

\chapter{Apéndice C: Componentes}
\renewcommand{\thepage}{C-\arabic{page}}
\setcounter{page}{1}

    \section{RP2040 Zero}
    \label{rp2040}
            \begin{figure}[!ht]
                \centering
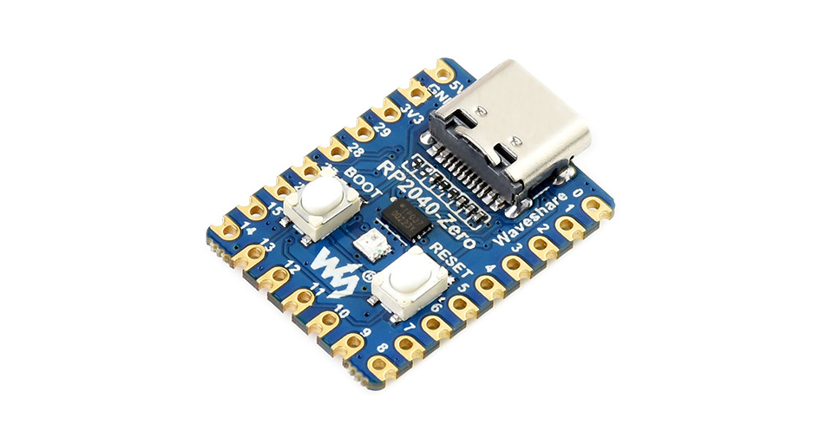
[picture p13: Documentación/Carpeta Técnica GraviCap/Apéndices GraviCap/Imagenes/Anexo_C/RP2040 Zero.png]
                
                \caption{RP2040 Zero}
                \label{fig:c1}
            \end{figure}
            
            Datos:\par
                \begin{itemize}[label=•]
                    \setlength{\itemindent}{2em}
                    
                    \item Chip microcontrolador RP2040 diseñado por Raspberry Pi en el Reino Unido\par
                    \item Procesador núcleo dual ARM Cortex M0+, con clock flexible que llega hasta los 133MHz\par
                    \item 264KB de SRAM, y 2MB de memoria Flash en la placa.
                    \item Conector USB-C, lo mantiene actualizado a los estándares actuales y más fácil de usar.\par
                    \item Los agujeros almenados permiten la soldadura directa a la placa.\par
                    \item USB 1.1 con soporte dispositivo/host.\par
                    \item Modos de suspención de bajo consumo y modo sleep.\par
                    \item Programación Drag-and-drop utilizando almacenaje en masa por USB.\par
                    \item 29 × pines GPIO multifunción (20× por vías externas, otros por puntos de soldadura).\par
                    \item 2 × SPI, 2 × I2C, 2 × UART, 4 × 12-bit ADC, 16 × canales de PWM controlables.\par
                    \item Clock y timer precisos en el chip.\par
                    \item Sensor de Temperatura.\par
                    \item Librerías     Accelerated floating-point en el chip.\par
                    \item 8 × Programmable I/O (PIO) state machines para soporte de periféricos personalizados.\par
                \end{itemize}
            
                Sitio Web: (\href{https://www.waveshare.com/wiki/RP2040-Zero}{https://www.waveshare.com/wiki/RP2040-Zero})\par
        
        \newpage
        
        \section{INA219}
        \label{ina219}
                \begin{figure}[!ht]
                    \centering
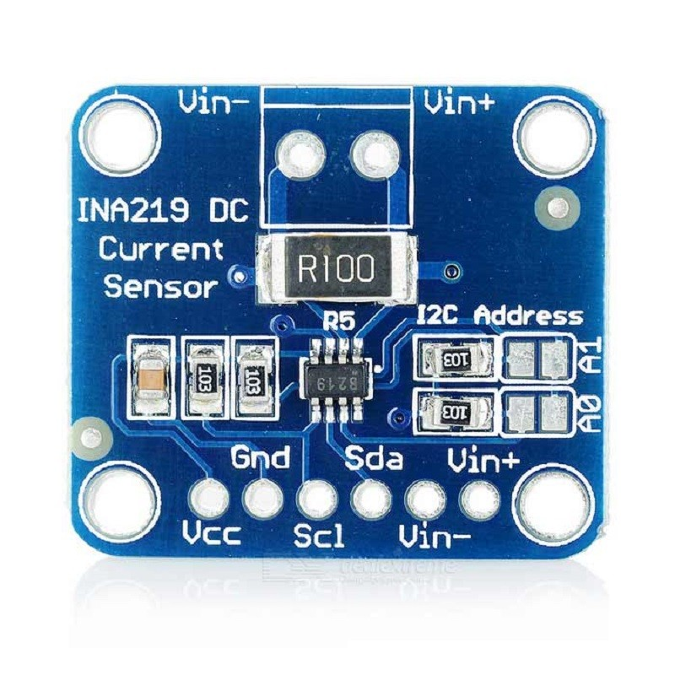
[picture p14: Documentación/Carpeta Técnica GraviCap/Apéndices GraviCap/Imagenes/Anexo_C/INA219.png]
                    
                    \caption{Módulo INA219}
                    \label{fig:c2}
                \end{figure}
            
                Datos:\par
            
                \begin{itemize}[label=•]
                    \setlength{\itemindent}{2em}
                    
                    \item Entrada de potencia: 3,0V-5,5V\par
                    \item Voltaje objetivo hasta +26V\par
                    \item Resistencia de detección de corriente de 0,1 ohm 1\% 2W\par
                    \item Medición de corriente de hasta ±3,2A, con resolución de ±0,8mA\par
                    \item Detecta voltajes de bus de 0 a 26 V\par
                    \item Interfaz compatible con I2C- o SMBus-\par
                    \item Se pueden promediar hasta 128 muestras para lograr filtrado en entornos ruidosos.\par
                    \item Dimensiones de la Placa: 0.8 x 0.9 Pulgadas (l x w x h)\par
                \end{itemize}
            
                Datasheet: (\href{https://www.alldatasheet.com/datasheet-pdf/pdf/249609/TI/INA219.html}{https://www.alldatasheet.com/datasheet-pdf/pdf/249609/TI/INA219.html})\par

        \newpage
        
        \section{LPD3806-360BM}
        \label{encoder}
        
                \begin{figure}[!ht]
                \centering
                
            \caption{LPD3806-360BM}
            \label{fig:c3}
        \end{figure}
        
            Datos:\par
            
            \begin{itemize}[label=•]
                \setlength{\itemindent}{2em}
                
                \item Pulsos: 600 p/r (600 pulsos/R monofasico, doble frecuencia de 4 a 2400 pulsos).\par
                \item Tension de Funcionamiento: 5V a 24V DC
                \item Eje: 6mm (Diametro) x 13mm (Largo)\par
                \item Dimensiones: 38mm x 35,5mm\par
                \item Salida de Pulso ortogonal rectangular con salida 2 fases AB\par
                \item Salida de colector abierto NPN\par
                \item Velocidad Mecanica Maxima: 5000rpm.\par
                \item Frecuencia de respuesta: 0-20kHz\par
            \end{itemize}
            
            Datasheet: (\href{https://www.alldatasheet.com/datasheet-pdf/pdf/1150705/ETC2/LPD3806-360BM.html}{https://www.alldatasheet.com/datasheet-pdf/pdf/1150705/ETC2/LPD3806-360BM.html}) (Está en Chino)\par

    \newpage
    
    \section{ESP8266 ESP-01S}
    \label{esp8266}
        \begin{figure}[!ht]
            \centering
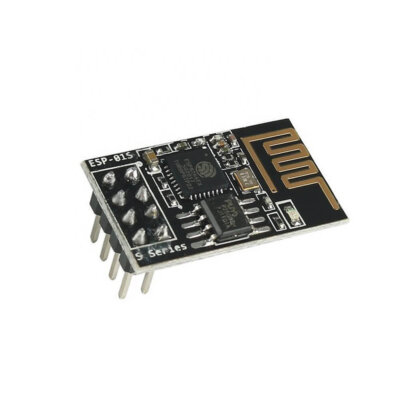
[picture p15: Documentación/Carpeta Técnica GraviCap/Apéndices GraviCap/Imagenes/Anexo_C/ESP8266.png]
            
            \caption{Módulo ESP8266 ESP-01S}
            \label{fig:c4}
        \end{figure}
        
        Datos:\par
        
        \begin{itemize}[label=•]
            \setlength{\itemindent}{2em}
            
            \item Voltaje de alimentación: 3.3 V. Este módulo no tolera 5 V.\par
            \item Comunicación tipo de interfaz: Serial, UART\par
            \item CPU de 32 bits\par
            \item Frecuencia de Reloj: 80MHz/160MHz\par
           \item Instruction RAM: 32KB\par
            \item Data RAM: 96KB\par
            \item Memoria Flash Externa: 4MB\par
            \item Soporte 3 modos: AP, STA, AP + STA\par
            \item Wi-Fi Direct (P2p), soft-AP\par
            \item Protocolos soportados: 802.11 b/g/n –  TCP/IP\par
            \item Soporte de red: 2,4 GHz\par
            \item Perfecto y simple en comandos AT\par
        \end{itemize}
            
        Datasheet: (\href{https://www.alldatasheet.com/datasheet-pdf/pdf/1424861/ETC/ESP8266.html}{https://www.alldatasheet.com/datasheet-pdf/pdf/1424861/ETC/ESP8266.html})\par

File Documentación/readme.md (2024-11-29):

# Documentación

&nbsp;&nbsp;&nbsp;&nbsp;&nbsp;&nbsp;La documentación en cualquier proyecto es una parte escencial del desarrollo, comercialización, distribución, entre otras cosas.<br>
&nbsp;&nbsp;&nbsp;&nbsp;&nbsp;&nbsp;Así, la documentación de GraviCap está dividida en 5 partes:<br>

- Carpeta Técnica.
- Manual de Usuario. 
- Bitácora Semanal.
- Compras.
- Elementos Faltantes.
  
## Recursos utilizados
- Overleaf
- CTAN

## Lenguaje utilizado  
&nbsp;&nbsp;&nbsp;&nbsp;&nbsp;&nbsp;LaTeX (Gracias al compilador [Overleaf](https://www.overleaf.com/about/features-overview))

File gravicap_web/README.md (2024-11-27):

# Página web 

Creamos una [página web](https://gravicap.vercel.app/)<br> para promocionar el proyecto y mostrarle al público de forma resumida y fácil de acceder una explicación del proyecto, un listado de integrantes y el trabajo que hizo cada uno, una galería para mostrar nuestro progreso y una sección para que se puedan contactar con nosotros de manera más directa. Junto a links para acceder directamente a nuestro instagram y github.

## Lenguajes utilizados 

- HTML
- CSS
- Vue.js

Se uso HTML y CSS para realizar la estructura de la página web, sus funciones y estilizarla tanto para computadoras como dispositivos móviles. Vue.js fue usado para separar los diferentes componentes de la página web en distintas secciones para acceder fácilmente a estas sin tener que recargar la página al seleccionarlas y que no se necesite scrollear en la página. 

## Componentes de la página web

La página web se divide en 4 componentes

- [Home](https://gravicap.vercel.app/home)<br>
Tiene un resúmen del proyecto y los beneficios de este, es el componente predeterminado al que se llega al buscar la página web.

- [Sobre Nosotros](https://gravicap.vercel.app/sobre_nosotros)<br>
Habla sobre nosotros como un grupo e indica el rol que cumplimos cada uno en este proyecto.

- [Galería](https://gravicap.vercel.app/galeria)<br>
Tiene imágenes del proceso de nuestro proyecto, las visitas a medios que tuvimos y nuestra participación en las ONIET.

- [Contáctanos](https://gravicap.vercel.app/contactanos)<br>
Por medio de w3schools generamos una llave para que cuando se rellene la forma que se encuentra en este componente, el mensaje con el mail y nombre de la persona, llegue a nuestro mail del proyecto así establecemos una línea de contacto más directa con quien lo desee.

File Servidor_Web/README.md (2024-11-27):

# Servidor Web

&nbsp;&nbsp;&nbsp;&nbsp;&nbsp;&nbsp;Este servidor recibe datos actualizados vía __UART__ desde la [RP2040-Zero](https://datasheets.raspberrypi.com/rp2040/rp2040-datasheet.pdf), 
los datos luego serán levantados por la [aplicación móvil](https://github.com/impatrq/gravicap/tree/main/GraviCap_app), un punto de acceso directo a la información del dispositivo en __Tiempo Real__ para el usuario.<br>
&nbsp;&nbsp;&nbsp;&nbsp;&nbsp;&nbsp;El programa del servidor es ejecutado por una [ESP8266-01](https://www.espressif.com/sites/default/files/documentation/esp8266-technical_reference_en.pdf).<br>
#### Lenguaje utilizado
  &nbsp;&nbsp;&nbsp;&nbsp;&nbsp;&nbsp;C++ (con soporte de [PlatformIO](https://docs.platformio.org/en/latest/)).<br>

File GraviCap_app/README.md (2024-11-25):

# Aplicación Móvil 
&nbsp;&nbsp;&nbsp;&nbsp;&nbsp;&nbsp; La aplicación móvil tiene como objetivo mostrarle al usuario los distintos tipos de valores de la batería en tiempo real. Esto lo hará por medio de pantallas destinadas a los valores e interacciones que necesite el usuario, contando con gráficos dinámicos en algunas pantallas.<br>
&nbsp;&nbsp;&nbsp;&nbsp;&nbsp;&nbsp; Para obtener los valores en tiempo real de la batería, la aplicación se comunica vía WiFi con el [servidor web](https://github.com/impatrq/gravicap/tree/main/Servidor_Web).<br>
# Recursos Utilizados 
[MarvelApp](https://marvelapp.com/) <br>
[Ionic](https://ionicframework.com/) <br>
[AndroidStudio](https://developer.android.com/?hl=es-419) <br>
# Lenguajes Utilizados 
React <br>
HTML <br>
CSS <br>
JavaScript <br>

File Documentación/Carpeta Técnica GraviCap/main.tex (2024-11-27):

% Establece la clase del documento y las especificaciones de la misma.
\documentclass[28pt, a4paper]{report}

%%%%%%%%%%%%%%%%%%%%%%%%%%%%%%%%%%%%%%%%%%%%%%%%%%%%%%%%%%%%%%%%%%%%%%%%%%%%%%%%%%%%%%%%%%%%%%%%%%%%%%%%%%%%%%%%%%%%%%%%%%%%%%%%%

% Establece el tamaño de los bordes de la página.
\usepackage[top=2cm, bottom=2cm, left=2cm, right=2cm]{geometry}
% Permite el uso de hipervínculos en el documento.
\usepackage{hyperref}
% Establece que el documento va a ser escrito en español (méxico).
\usepackage[spanish]{babel}
% Permite el control sobre la Tabla de Contenidos, Figuras, etc.
\usepackage{tocloft}
% Fuente y Tipografía.
\usepackage[sfdefault,lf]{carlito}
% Asegura el uso de "Unicode Transformation Format 8-bit" para asegurar el uso de carácteres modernos.
\usepackage[utf8]{inputenc}
% Permite el uso de espaciado entre carácteres, líneas, etc.
\usepackage{setspace}
% Permite el uso de ítems con diferente forma.
\usepackage{enumitem}
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

\newcounter{subsubsubsection}[subsubsection]
\renewcommand\thesubsubsubsection{\thesubsubsection.\arabic{subsubsubsection}}
\renewcommand\theparagraph{\thesubsubsubsection.\arabic{paragraph}}

\titleformat{\subsubsubsection}
  {\normalfont\normalsize\bfseries}{\thesubsubsubsection}{1em}{}
\titlespacing*{\subsubsubsection}
{0pt}{3.25ex plus 1ex minus .2ex}{1.5ex plus .2ex}

\makeatletter
\renewcommand\paragraph{\@startsection{paragraph}{5}{\z@}%
  {3.25ex \@plus1ex \@minus.2ex}%
  {-1em}%
  {\normalfont\normalsize\bfseries}}
\renewcommand\subparagraph{\@startsection{subparagraph}{6}{\parindent}%
  {3.25ex \@plus1ex \@minus .2ex}%
  {-1em}%
  {\normalfont\normalsize\bfseries}}
\def\toclevel@subsubsubsection{4}
\def\toclevel@paragraph{5}
\def\toclevel@paragraph{6}
\def\l@subsubsubsection{\@dottedtocline{4}{7em}{4em}}
\def\l@paragraph{\@dottedtocline{5}{10em}{5em}}
\def\l@subparagraph{\@dottedtocline{6}{14em}{6em}}
\makeatother

\setcounter{secnumdepth}{4}
\setcounter{tocdepth}{4}

%%%%%%%%%%%%%%%%%%%%%%%%%%%%%%%%%%%%%%%%%%%%%%%%%%%%%%%%%%%%%%%%%%%%%%%%%%%%%%%%%%%%%%%%%%%%%%%%%%%%%%%%%%%%%%%%%%%%%%%%%%%%%%%%%

% Establece las condiciones para los hipervínculos.
\hypersetup{colorlinks=true,linkcolor=medium_violet,filecolor=dark_violet,urlcolor=light_violet,pdftitle={Carpeta Técnica GraviCap},pdfpagemode=FullScreen,}

%%%%%%%%%%%%%%%%%%%%%%%%%%%%%%%%%%%%%%%%%%%%%%%%%%%%%%%%%%%%%%%%%%%%%%%%%%%%%%%%%%%%%%%%%%%%%%%%%%%%%%%%%%%%%%%%%%%%%%%%%%%%%%%%%

% Establece el estilo de la página para permitir el uso de encabezados y pies de página.
\pagestyle{fancy}
% Establece el uso de encabezados y pies de página.
\fancyhf{}
% Establece el contenido de la parte izquierda del encabezado.
\lhead{\footnotesize \textcolor{dark_violet}{\textbf{GraviCap}} - \the\year{}}
% Establece el contenido de la parte central del encabezado.
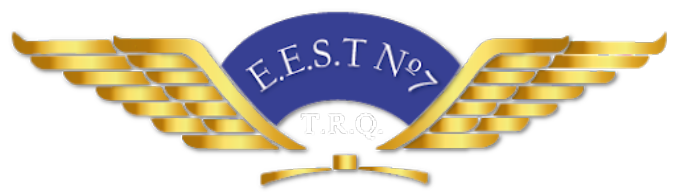
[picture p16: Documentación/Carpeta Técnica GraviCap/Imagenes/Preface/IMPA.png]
\chead{}
% Establece el contenido de la parte de derecha del encabezado.
\rhead{\footnotesize E.E.S.T N°7 IMPA "T.R.Q."}
% Establece el contenido de la parte central del pie de página.
\cfoot{\large \thepage}

%%%%%%%%%%%%%%%%%%%%%%%%%%%%%%%%%%%%%%%%%%%%%%%%%%%%%%%%%%%%%%%%%%%%%%%%%%%%%%%%%%%%%%%%%%%%%%%%%%%%%%%%%%%%%%%%%%%%%%%%%%%%%%%%%%

% Establece que dentro de la tipografía "Carlito" se use la variante "OsF".
\renewcommand*\oldstylenums[1]{\carlitoOsF #1}
% Establece el tamaño del pie de página.
\renewcommand{\footrulewidth}{0.4pt}
% Establece que en la tabla de contenidos se use una línea de puntos para marcar el número de página.
\renewcommand{\cftsecleader}{\cftdotfill{\cftdotsep}}
% Establece un color con los valores 102, 19, 154 en RGB.
\providecolor{medium_violet}{RGB}{102,19,154}
% Establece un color con los valores 169, 68, 238 en RGB.
\providecolor{light_violet}{RGB}{169,68,238}
% Establece un color con los valores 81, 9, 129 en RGB.
\providecolor{dark_violet}{RGB}{81,9,129}

\definecolor{codegreen}{rgb}{0,0.6,0}
\definecolor{codegray}{rgb}{0.5,0.5,0.5}
\definecolor{codepurple}{rgb}{0.58,0,0.82}
\definecolor{backcolour}{rgb}{0.95,0.95,0.92}

%%%%%%%%%%%%%%%%%%%%%%%%%%%%%%%%%%%%%%%%%%%%%%%%%%%%%%%%%%%%%%%%%%%%%%%%%%%%%%%%%%%%%%%%%%%%%%%%%%%%%%%%%%%%%%%%%%%%%%%%%%%%%%%%%

\lstdefinestyle{mystyle}{
    backgroundcolor=\color{backcolour},   
    commentstyle=\color{codegreen},
    keywordstyle=\color{magenta},
    numberstyle=\tiny\color{codegray},
    stringstyle=\color{codepurple},
    basicstyle=\ttfamily\footnotesize,
    breakatwhitespace=false,         
    breaklines=true,                 
    captionpos=b,                    
    keepspaces=true,                 
    numbers=left,                    
    numbersep=5pt,                  
    showspaces=false,                
    showstringspaces=false,
    showtabs=false,                  
    tabsize=2
}

\lstset{style=mystyle}

%%%%%%%%%%%%%%%%%%%%%%%%%%%%%%%%%%%%%%%%%%%%%%%%%%%%%%%%%%%%%%%%%%%%%%%%%%%%%%%%%%%%%%%%%%%%%%%%%%%%%%%%%%%%%%%%%%%%%%%%%%%%%%%%%

\begin{document}
\begin{titlepage}

        \begin{center}      
            \begin{figure} [!ht]
                \centering
                \includegraphics [width=9cm]{Imagenes/Preface/Logo-Nombre.png}
                \label{Logo-Nombre}
            \end{figure}
            
                \vspace{0.5cm}
                {\LARGE\textbf{{\textcolor{dark_violet}{\textbf{\textit{Una forma de elevar tu energía}}}}}}\par
                \vspace{0.5cm}
                
            {\Huge\textbf{Carpeta Técnica}}\par
                \vspace{1cm}
                
            {\LARGE\textbf{7mo 1ra Comisión A}}\par
                \vspace{0.2cm}
                
            {\LARGE\textbf{Año \the\year}}\par
                \vspace{1cm}
                
            {\Large\textbf{{Alvarez Mollo, Fausto}}}\par
            
            {\Large\textbf{{Bianqui Kronemberger, Mariano Joaquín}}}\par
            
            {\Large\textbf{{Calleja, Tomás Joaquín}}}\par
            
            {\Large\textbf{{Donatti, Augusto}}}\par
            
            {\Large\textbf{{Felizia, Tatiana Milena}}}\par
            
            {\Large\textbf{{Sofía, Gabriel Jerónimo Takashi}}}\par
                \vspace{1.5cm}
                
            \begin{figure} [!ht]
                \centering
                \includegraphics [width=7cm]{Imagenes/Preface/IMPA.png}
                \label{IMPA}
            \end{figure}
            
        \end{center}
        
    \end{titlepage}
    
%%%%%%%%%%%%%%%%%%%%%%%%%%%%%%%%%%%%%%%%%%%%%%%%%%%%%%%%%%%%%%%%%%%%%%%%%%%%%%%%%%%%%%%%%%%%%%%%%%%%%%%%%%%%%%%%%%%%%%%%%%%%%%%%%%%%%%%%%%%%%%%
    \tableofcontents
    \newpage
%%%%%%%%%%%%%%%%%%%%%%%%%%%%%%%%%%%%%%%%%%%%%%%%%%%%%%%%%%%%%%%%%%%%%%%%%%%%%%%%%%%%%%%%%%%%%%%%%%%%%%%%%%%%%%%%%%%%%%%%%%%%%%%%%%%%%%%%%%%%%%%

\include{Archivos/Preambulo}
\include{Archivos/Introduccion}
\include{Archivos/Estructura}
\include{Archivos/MPPT}
\include{Archivos/Software}
\include{Archivos/Hardware}
\include{Archivos/Aplicacion}
\include{Archivos/Pagina}
\include{Archivos/Futuro}
\include{Archivos/Bibliografia}

\end{document}

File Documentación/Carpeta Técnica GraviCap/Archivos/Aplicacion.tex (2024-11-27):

\chapter{Aplicación}

    \section{Función de la aplicación}
        La aplicación móvil tiene como objetivo mostrarle al usuario los distintos tipos de valores de la batería en tiempo real. Esto lo hará por medio de pantallas destinadas a los valores e interacciones que necesite el usuario, contando con gráficos interactivos. Los datos mostrados en la aplicación son subidos desde una base de datos. Contando también con una sección para contactarnos, por medio de nuestras redes sociales y página web.\par
        Con esta aplicación, el usuario podrá saber, en todo momento, los valores que necesite de la batería, como por ejemplo, la entrega que tiene la batería hacia el dispositivo que esté alimentando o, para un perfil más técnico, valores del panel solar y gráficos para más detalles sobre la misma.\par

    \section{Desarrollo del mockup de la aplicación}
    
        \subsection{Mockup}
            	Para poder desarrollar la aplicación, se necesita tener un Mockup. Su función es proveer al desarrollador el prototipo de funcionamiento, planteado de forma ilustrativa, el cual, da un primer vistazo estético, funcional e informativo de cómo será la misma. \par
                Esto conlleva plantear el diseño, e información que contendrá la aplicación , para que, posteriormente, el desarrollo final de la aplicación, se base en el Mockup, siendo de esta forma, más cómodo y práctico poder desarrollarla.\par
                La página que se designó para realizar el Mockup, fue “\href{https://marvelapp.com}{Marvel}”.\par
                Dentro de este, pueden haber varios cambios según vaya avanzando y se necesite, ya que, al fin y al cabo, es a modo ilustrativo para después poder desarrollar la aplicación final.\par
                
                \begin{figure}[H]
                    \centering
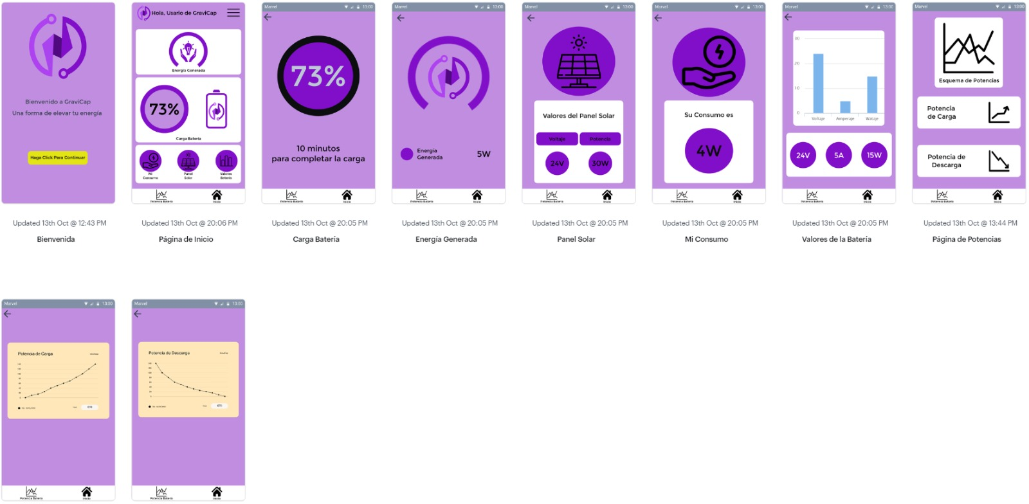
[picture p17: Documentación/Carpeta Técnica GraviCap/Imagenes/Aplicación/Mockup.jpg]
                    
                    \caption{Mockup de la aplicación.}
                    \label{fig:a14}
                \end{figure}
                
            \subsection{UI/UX}
                La \textbf{UX} (Experiencia de Usuario) es la experiencia integral y el conjunto de interacciones que tienen los usuarios con la misma.\par
                En cuanto a la \textbf{UI} (Interfaz de Usuario) consiste en toda la arquitectura de información, patrones y diferentes elementos visuales que nos permitan explorar la funcionalidad de la aplicación de forma eficaz y gratificante.\par
                Con esto, el usuario podrá tener una interacción “amigable” con la aplicación, siendo más cómodo y práctico moverse dentro de la misma para ver lo que necesite.\par
                La diferencia entre estos, es que la UX se centra en la manera en que el usuario interactúa con el producto de manera eficaz y, por otro lado, la UI busca ofrecer una experiencia estética satisfactoria.\par

            \subsection{User Journey}
                Para el desarrollo de la aplicación se planteó utilizar como metodología, una “jornada de usuario”. Esta metodología, plantea un mapa de recorrido del usuario en nuestra aplicación, representando así, su experiencia visual e interactiva con la misma. Pudiendo así, plantear el desarrollo del Mockup enfocándonos en el proceso que realizaría nuestro usuario dentro de la aplicación y su perspectiva.\par
                El proceso para esta metodología es buscar la empatía con el usuario, comprendiendo la relación y puntos de contacto que este tiene. Analizar sus acciones y procesos, para así, determinar lo que necesita. Con esto, se puede generar una mejor experiencia para el usuario y un proceso más eficiente.\par
                Facilita tanto el desarrollo de la aplicación como el proyecto en sí, generando una experiencia del usuario y requerimientos para el mismo. También se relaciona directamente con la UI/UX y facilita un mejor y cómodo planteamiento para las mismas.\par
                Esta herramienta o metodología, nos permite generar un usuario para así comprender y mejorar su experiencia dentro de la aplicación, así también, dándonos un mejor desarrollo dentro de nuestro proyecto.\par

        \section{Estructura de la Aplicación}
        
            \subsection{Editor de Código y Framework}
                Para el desarrollo de la aplicación, se utilizó el editor de código “Visual Studio Code”, en conjunto con “\href{https://ionicframework.com}{Ionic}" un framework de código abierto, proporcionandonos comodidad y amplias opciones de herramientas para el desarrollo, conteniendo varias opciones para la implementación en varios lenguajes.
                
            \subsection{Lenguajes Utilizados}
                Los lenguajes utilizados fueron HTML, CSS, JS y, como principal, React. Siendo este último, el lenguaje principal para el uso de las herramientas que nos provee Ionic.\par
                
            \subsection{Componentes}
        
                \subsubsection{WelcomePage.tsx}
                
                    Este componente es el primero que se ve al iniciar la aplicación, su función consta de darle una pequeña bienvenida al usuario, con nuestro logo y \textit{slogan}, explicando un poco sobre la batería, el proyecto, la funcionalidad de la aplicación y un botón que lo envía a la pantalla de inicio una vez que el usuario quiera.\par
    
                    \begin{figure} [H]
                        \centering
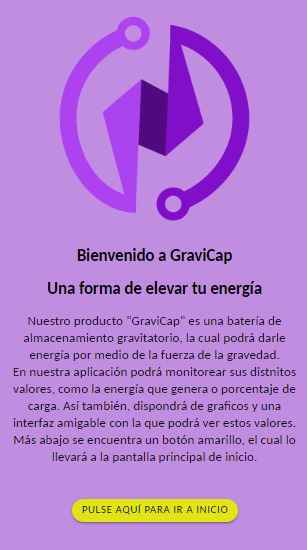
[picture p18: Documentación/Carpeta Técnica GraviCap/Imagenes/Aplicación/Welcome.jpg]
                        
                        \caption{Página de Bienvenida}
                        \label{fig:a1}
                    \end{figure}
                
                \subsubsection{StartPage.tsx}
                    Una vez vista la pantalla de bienvenida, el usuario es reenviado hacia la pantalla de inicio, la cual, es la pantalla principal de la aplicación, esta contiene los botones con links hacia las distintas pantallas de valores.En la parte inferiror izquierda de la página encontramos un botón amarillo de tamaño pequelo el cual le permite al usuario redirigirse hacia la pantalla de gráficos de potencia de la batería.\par
                    En el apartado de arriba a la derecha encontramos un botón de información, el cual contiene los links hacia nuestro contacto y diversas redes sociales.\par
                    
                    \begin{figure} [H]
                        \centering
                        \begin{subfigure}{0.4\textwidth}
                            \centering
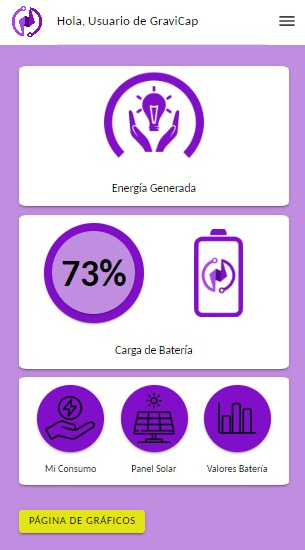
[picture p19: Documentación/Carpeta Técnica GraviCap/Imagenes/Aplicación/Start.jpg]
                            
                            \caption{Página de Inicio}
                            \label{fig:a2.1}
                        \end{subfigure}
                        \begin{subfigure}{0.4\textwidth}
                            \centering
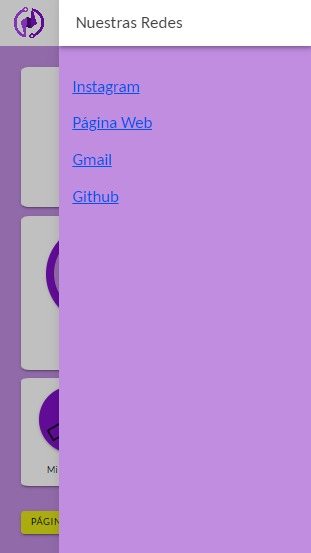
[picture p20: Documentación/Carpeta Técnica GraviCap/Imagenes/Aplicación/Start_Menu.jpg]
                            
                            \caption{Menú de Inicio}
                            \label{fig:a2.2}
                        \end{subfigure}
                        \hfill
                                
                        \caption{Ambas partes de la Página de Inicio}
                        \label{fig:a2}
                        \end{figure}
                
                \subsubsection{GeneratedEnergy.tsx}
                    Este componente contiene un valor importante y recurrente para el usuario, el cual es la energía generada por la batería. Este valor le provee al usuario el valor de cuánta potencia está entregando hacia su dispositivo.\par
                    En esta pantalla disponemos de un gráfico circular referenciando el valor de potencia de energía generada de la batería.\par
                    En la parte inferior encontramos el color referenciando el valor del gráfico con un texto plasmando el valor numérico textualmente con su unidad (Watt).\par
    
                    \begin{figure} [H]
                        \centering
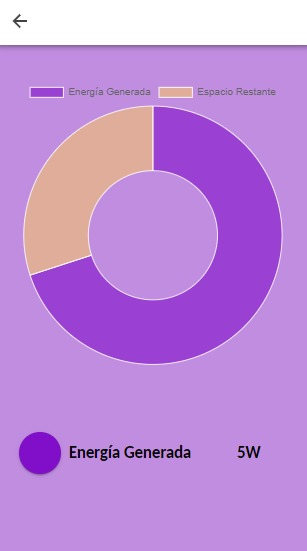
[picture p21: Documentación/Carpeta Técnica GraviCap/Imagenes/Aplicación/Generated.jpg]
                        
                        \caption{La cantidad de energía generada (Los valores son de referencia)}
                        \label{fig:a3}
                    \end{figure}
                
                \subsubsection{BatteryCharge.tsx}
                    Para el usuario, también es importante saber cuál es la carga de la batería, es decir, en este caso, si está en su punto más alto o más bajo. Este valor se basa en un porcentaje, el cual nos indica la posición del peso de la batería, que se traduce en un valor porcentual para el usuario. Por ejemplo, el 100\% de la batería, se da cuando el peso está en su punto más alto, ya habiendo almacenado la energía potencial gravitatoria. Por lo tanto, el 0\% referencia cuando el peso está en su punto más bajo, ya habiendo descargado toda la batería.\par
                    Este apartado también cuenta con el tiempo que falta para que la batería llegue a completar su carga.\par
    
                    \begin{figure} [H]
                        \centering
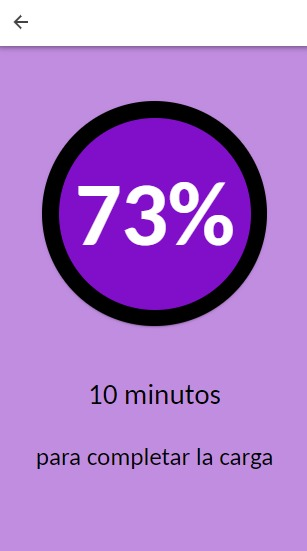
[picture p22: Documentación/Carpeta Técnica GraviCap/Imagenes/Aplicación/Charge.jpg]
                        
                        \caption{Carga de la batería (Los valores son de referencia)}
                        \label{fig:a4}
                    \end{figure}
                
                \subsubsection{MyConsumption.tsx}
                    El usuario también necesita saber el consumo de su dispositivo. Ese es el funcionamiento de este componente. Dándole el valor en unidad de potencia.\par
    
                    \begin{figure} [H]
                        \centering
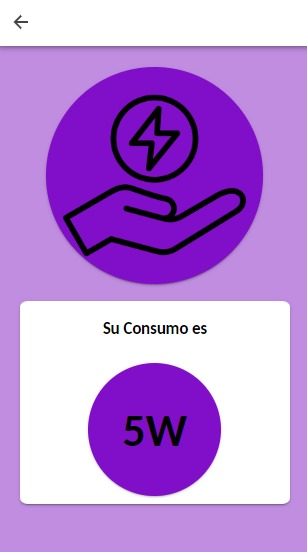
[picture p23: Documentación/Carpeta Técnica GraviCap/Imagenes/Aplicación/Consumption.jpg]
                        
                        \caption{El consumo del usuario (Los valores son de referencia)}
                        \label{fig:a5}
                    \end{figure}
                
                \subsubsection{SolarPanel.tsx}
                    Para saber los valores de entrega del panel solar, el usuario puede verlos dentro de la pantalla del panel solar.\par
                    Los valores que podemos ver son el voltaje que entrega y su potencia. Todo esto en tiempo real.\par
    
                    \begin{figure} [H]
                        \centering
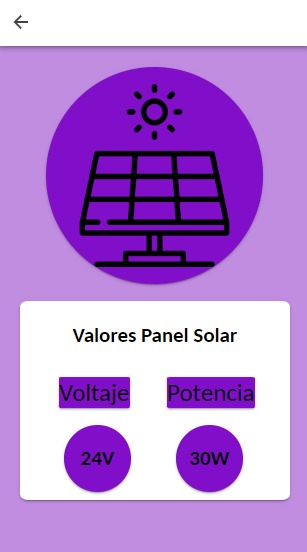
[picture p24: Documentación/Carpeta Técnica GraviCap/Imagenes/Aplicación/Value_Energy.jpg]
                        
                        \caption{Valor del panel solar utilizado (Los valores son de referencia)}
                        \label{fig:a6}
                    \end{figure}
                
                \subsubsection{BatteryValues.tsx}
                    Para registrar la batería y sus valores varios, en la pantalla de valores de batería el usuario podrá ver valores como Voltaje, Corriente y Potencia de la batería.\par
    
                    \begin{figure} [H]
                        \centering
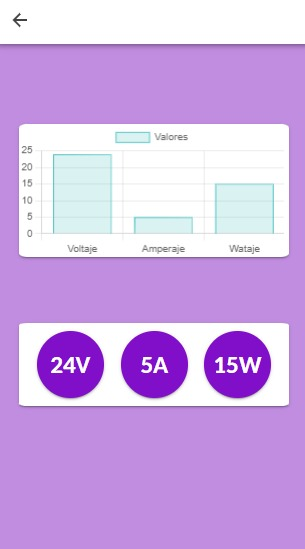
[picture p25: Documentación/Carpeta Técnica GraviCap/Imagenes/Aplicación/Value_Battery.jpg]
                        
                        \caption{Valor de la batería (Los valores son de referencia)}
                        \label{fig:a7}
                    \end{figure}

                \subsubsection{GraphicsPage.tsx}
                    En este apartado, el cual el usuario puede acceder desde el botón amarillo de la página de inicio, encontraremos dos botones los cuales contienen los gráficos de carga y descarga de la batería.\par
    
                    \begin{figure} [H]
                        \centering
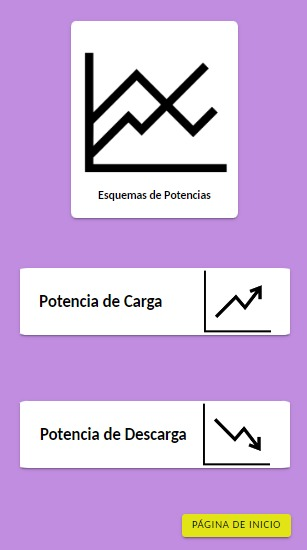
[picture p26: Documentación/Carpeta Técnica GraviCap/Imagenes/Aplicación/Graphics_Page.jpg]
                        
                        \caption{Página de Gráficos}
                        \label{fig:a8}
                    \end{figure}

                \subsubsection{ChargingPowerGraphics.tsx}
                    En esta pantalla encontramos un gráfico ascendente, el cual se basa en la potencia que entrega la batería en función del tiempo cuando el peso está en su momento de ascenso.\par
    
                    \begin{figure} [H]
                        \centering
                        
                        \caption{Gráfico de Carga (Los valores son de referencia)}
                        \label{fig:a9}
                    \end{figure}

                \subsubsection{DischargePowerGraphics.tsx}
                    Esta pantalla actúa de igual forma que la anterior, encontraremos un gráfico descendente el cual se basa en la potencia que entrega la batería en función del tiempo.\par
                    Este funciona cuando la batería se encuentra en estado de descarga, es decir, cuando está descendiendo.\par
    
                    \begin{figure} [H]
                        \centering
                        
                        \caption{Gráfico de Descarga (Los valores son de referencia)}
                        \label{fig:a10}
                    \end{figure}

                \subsubsection{Buttons.tsx}
                    Este componente es un botón de tamaño pequeño amarillo ubicado en la parte inferior de la página de inicio, el cual está declarado con una ruta de navegación que permite conectar la página principal de inicio con la página de gráficos de potencia de la batería.\par 
                    También hay un botón del mismo estilo en la página de gráficos para poder volver hacia la pantalla principal de inicio si se necesita.\par 
                    Con esto, damos una forma eficiente de visualización de valores entre páginas por medio de estos botones.\par

                    \begin{figure}[H]
                        \centering
                        \begin{subfigure}{0.4\textwidth}
                            \centering
                            
                            \caption{Botón para volver a la Página de Inicio}
                            \label{fig:a15.1}
                        \end{subfigure}
                        \begin{subfigure}{0.4\textwidth}
                            \centering
                            
                            \caption{Botón para volver la página de Gráficos}
                            \label{fig:a15.2}
                        \end{subfigure}
                        \hfill
                                
                        \caption{Ambas partes de la Página de Inicio}
                        \label{fig:a20}
                        \end{figure}
                    
                \subsubsection{Tabs.tsx}
                    Este componente es la barra de botones que se encuentra en la parte de abajo, este contiene un botón que te redirecciona hacia la pantalla de inicio y otra que te redirecciona hacia la parte los gráficos de potencia. Dándole una mayor accesibilidad al usuario hacia las pantallas del Tab.\par

                \subsubsection{main.tsx}
                    El main es un componente el cual no es visible, dentro de la aplicación. Este se encarga de poder ejecutar las rutas declaradas dentro del archivo App.tsx.\par

                \subsubsection{App.tsx}
                    Este componente tampoco es visible, ya que se encarga de declarar las rutas dentro de la aplicación. Por ejemplo, puede realizar que al abrir la aplicación, redireccione al usuario hacia la pantalla de bienvenida.\par
                
        \section{Desarrollo}
            Para el desarrollo de la aplicación, se descargó \textbf{Ionic}, configurando su descarga para la utilización de herramientas y templates con el lenguaje de programación de \textbf{React}. Para poder programar y utilizar las herramientas descargadas se utilizó el editor de código de \textbf{Visual Studio Code}.\par 
            \subsection{Base de Datos}
                Teniendo como base de desarrollo el Mockup, facilita la programación de la misma. También cabe resaltar que mediante se desarrolla la aplicación en sí, el Mockup puede ir variando o la aplicación puede no ser completamente fiel estética y visualmente al mismo, quedando la aplicación final, diferente al Mockup, esto ya que se utiliza como una primera base.\par 
                Mediante el proceso se encuentran nuevas herramientas que se adapten mejor a las necesidades del momento, reescribiendo o modificando el Mockup según se requiera para una mejor versión de la aplicación.\par
                
            \subsection{Creación de Archivos}
                Se crearon los distintos archivos que funcionarán como componentes para la creación de las pantallas de la aplicación, desarrollando y programando así la estructura de cada uno, importando las carpetas y herramientas para cada archivo.\par

            \subsection{Herramientas de Ionic}
                Para el desarrollo de programación de los archivos se necesitó tener conocimientos dentro del lenguaje de HTML para poder programar su estructura y combinarse con el lenguaje principal React y las herramientas que provee, creando así, componentes .tsx como archivos principales para el desarrollo. En cuanto a las herramientas que nos provee Ionic, se investigó en el Framework sobre sus templates e información del uso de las herramientas más convenientes para el desarrollo de los archivos. Para poder estilizarlos según queramos, se necesitó también tener conocimientos en CSS. Para los gráficos, importados de carpetas, se necesitó tener conocimientos básicos en JavaScript.\par
                
                \subsubsection{IonApp}
                    Para la creación de los archivos, se necesita empezar con una constante o función, en la cual iremos desarrollando el código para la creación de las pantallas, así como declarar primeramente una herramienta IonApp la cual contendrá el código y los elementos de la aplicación de Ionic, solamente se declara uno en el archivo que queramos considerar como principal.\par
                
                \subsubsection{IonContent}
                    Otro componente importante para el desarrollo es declarar un IonContent el cual actúa de contenedor principal de los componentes de la aplicación, dando así, un área única para el contenido por fuera del Header.\par
                
                \subsubsection{IonHeader y IonMenu}
                    IonHeader componente que actúa de barra superior central, conteniendo componentes tales como iconos, botones y texto (vistos en el Header de la pantalla de Inicio). En este mismo también se declara el componente IonMenu, un botón de información lateral ubicado en la parte superior derecha de la pantalla de inicio, proporcionando los links hacia nuestras redes sociales, contacto y página web.\par
                
                \subsubsection{IonCard}
                    Un componente muy utilizado es el de IonCard visto en gran parte en la pantalla de inicio y utilizado en otros archivos. Actuando de contenedor de otros componentes y, a su vez, dándole una mejor estética, actuando, como dice su nombre, como una carta. Modificándose en cuanto a estilos y formas con CSS, pueden actuar de contenedores circulares, también vistos en los contenedores de "Mi Consumo", "Panel Solar" y "Valores de Batería" en la pantalla de inicio. También dándole un recuadro en las páginas de gráficos, y actuando como "botones" (declarados con el componente de NavLink los cuales, al clickearlos, nos redireccionan hacia otra pantalla.\par
                    
                \subsubsection{IonNavLink y IonBackButton}
                    Con los archivos desarrollados con sus componentes y estructuras, para el movimiento del usuario por las diferentes pantallas de estas, estos necesitan un enrutamiento para la conexión entre sí. Para esto, los componentes que provee Ionic como botones (ion-button) o cartas (ion-card) se los programó con la función de IonNavLink, funciona como un enrutamiento, el cual realiza que al clickear un botón o carta nos redireccione hacia otro componente/archivo que le designemos. Con esto, el Usuario se puede movilizar dentro de la aplicación hacia donde necesite. Así también como se redirecciona hacia un componente, puede volver hacia atrás a la pantalla anterior, esto con la herramienta IonBackButton.\par
                    
                \subsubsection{IonButton}
                    Para una mejor interacción y movimiento del usuario dentro de la aplicación, se implementaron botones (ion-button). Por ejemplo, en la pantalla de Bienvenida. Otros ubicados en la parte inferior de la página de Inicio y de Gráficos la cual le permite al usuario moverse de una forma más eficiente entre las mismas. Estos cumplen la función de redireccionar al usuario hacia su determinada pantalla, dándole posibilidad de visualizar otras pantallas y obtener otro tipo de información.\par
                    
                \subsubsection{Formato SmartPhone}
                    Ionic también nos provee una herramienta para poder ver el desarrollo del archivo que estemos programando dentro de Visual Studio Code en forma de un SmartPhone. Con esta función se facilita poder programar cada componente estructural para el desarrollo final.\par
                    
                    \begin{figure}[H]
                        \centering
                        
                        \caption{Imagen de Referencia de la función de Smartphone}
                        \label{fig:a15}
                    \end{figure}
        
                    Con los archivos desarrollados con sus componentes y estructuras, para el movimiento del usuario por las diferentes pantallas de estas, los componentes necesitan un enrutamiento para la conexión entre sí. Para esto, los componentes que provee Ionic como botones (\textit{ion-button}) o cartas (\textit{ion-card}) se los programó con la función de \textit{IonNavLink}, funciona como un enrutamiento, el cual realiza que al clickear un botón o carta nos redireccione hacia otro componente/archivo que le designemos. Con esto, el Usuario se puede movilizar dentro de la aplicación hacia donde necesite. Así también como se redirecciona hacia un componente, puede volver hacia atrás a la pantalla anterior, esto con la herramienta \textit{IonBackButton}.\par
                        
                    El usuario, en la pantalla de inicio, en la parte superior derecha de la misma, dispone de un botón de información, el cual, le proveerá información de nuestras redes sociales y contacto.\par
                    Para un mejor movimiento del usuario dentro de la aplicación, se implementó la herramienta \textit{Tabs} (\textit{ion-tabs}). Esta es una barra ubicada en la parte inferior la cual le permite al usuario moverse de una forma más eficiente, conteniendo iconos, los cuales actúan de botones para redireccionar al usuario hacia su determinada pantalla, dándole posibilidad de visualizar otras pantallas y obtener otro tipo de información.\par
                    Una vez teniendo todos los archivos programados con sus respectivas estructuras y componentes, se debe añadir estilos, darle forma a los componentes que queramos, colores y tamaños, dándoles así el vistazo estético requerido planteado en el Mockup. Para esto, cada componente necesita sus estilos, creándose así un archivo \textit{CSS} individual para cada uno. Estos se programan y se importan al archivo que se requiera, modificando su estructura y tamaños dándole un mejor acabado estético para el usuario.\par
                
            \subsection{Estilos y CSS}
                Una vez teniendo todos los archivos programados con sus respectivas estructuras y componentes, se debe añadir estilos, darle forma a los componentes que queramos, colores y tamaños, dándoles así el vistazo estético requerido planteado en el Mockup. Para esto, cada componente necesita sus estilos, creándose así un archivo CSS individual para cada uno. Estos se programan y se importan al archivo que se requiera, modificando su estructura y tamaños dándole un mejor acabado estético para el usuario.\par
                
            \subsection{Gráficos}
                Para el desarrollo de los gráficos dentro de la aplicación, se utilizaron las carpetas de \textbf{charts.js} y \textbf{react-chartjs-2}. De estas carpetas, importamos los tipos de gráficos que necesitemos para, posteriormente, programarlos y darles forma con los valores que registre la base de datos. Los tipos de gráficos que se utilizaron fueron: “\textit{Doughnut}” (circular); “\textit{Bar}” (columna) y “\textit{Line}” (línea).\par
                Para esto, se creó un archivo diferente para el desarrollo de cada gráfico para, posteriormente, importarlo hacia los archivos de los gráficos. Estos archivos, al ser JavaScript, los desarrollamos en formato .jsx.\par

                \subsubsection{Tipos de Gráficos Utilizados}
                \begin{itemize} [label=•]
                \setlength{\itemindent}{1.5em}
                
                    \item Doughnut\par
                        Este gráfico fue utilizado en el apartado de la Pantalla de Energía generada, dándonos un gráfico circular el cual se adapta al valor de energía que genere la batería.\par
                        
                    \item Bar\par
                        Para que el usuario pueda ver los valores cómodamente, además de tener una referencia de su magnitud, se usó este tipo de gráfico, el cual nos da los valores referenciados en columnas.\par
                        Estos valores son el Voltaje, Amperaje y Wataje (potencia) de la batería.\par
                        Este gráfico se utilizó en la Pantalla de Valores de la Batería.\par
                        
                    \item Line\par
                        Dentro de los gráficos de potencia podemos observar 2 gráficos del mismo tipo, siendo estos de línea. Para referencia el valor de potencia de la batería en función del tiempo se utilizó este tipo de gráfico.\par
                        Para la potencia de carga siendo un gráfico de línea ascendente y para la Potencia de descarga siendo un gráfico del mismo tipo pero descendente.\par
                \end{itemize}
                
            \subsection{Servidor}
                El microcontrolador utilizado para la creación del servidor, fue una ESP8266, comunicándose con la aplicación por medio de WiFi.\par
                Para el desarrollo de código se utilizó C++ con un sistema de detección del usuario al servidor conectado dentro de la misma red WiFi.\par
                Dentro del servidor se obtienen los valores y datos de los sensores de la etapa de control, dándonos así, valores de corriente; tensión; voltaje y carga de los 4 sensores utilizados.\par
                Cada sensor contiene información de datos diferentes, destinados a sensar específicamente una sección de la batería, como el panel solar, el consumo de la batería, el consumo de usuario y la potencia de la placa MPPT.\par
                Al ser 4 sensores con información de datos diferentes, para una petición más cómoda de datos, realizamos solicitudes individuales a cada uno de los sensores por separado.
                Cuando se realice una solicitud dentro del servidor y sea correcta y aceptada, este está configurado para contestar mandando los valores en formato de archivo json mandando un \textit{string} con los valores.\par
                Dentro del desarrollo de la aplicación, para pedir los datos de los sensores dentro de los archivos de las pantalla, realizamos un fetch el cual solicitará los datos en forma de GET a la IP del servidor al sensor específico que le indiquemos.\par
                Una vez realizado el fetch, obtendremos todos los valores del sensor al cual le indicamos la solicitud. Posteriormente, para mostrar los datos que necesitemos dentro de la pantalla de la aplicación, declaramos una variable la cual contendrá el dato específico que necesitemos del sensor recibido y la utilizamos dentro de la aplicación, mostrando el valor dentro del dispositivo móvil.\par

            \newpage
            
            \subsection{Android Studio}
                Una vez teniendo todo el desarrollo de código dentro de Visual Studio Code, realizamos el vistazo de la aplicación dentro de un dispositivo móvil android. Para lograr esto, utilizamos Android Studio el cual nos permitió realizar la conversión de nuestro proyecto de desarrollo en una aplicación móvil ejecutable dentro de nuestro dispositivo móvil android. Con esto, ya tenemos el vistazo final de la aplicación dentro de un dispositivo móvil, solamente pudiendo variar los tamaños de la aplicación debido a la resolución que tenga cada dispositivo donde se descargue.\par
                Con esto, se pudo modificar los tamaños para adaptarlo lo mejor posible teniendo de referencia un celular con la aplicación.\par
                Para una mejor estética, Android Studio nos permite modificar el nombre a la aplicación vista en el dispositivo móvil y también el logo que tendrá, dándonos así la posibilidad de modificarlo a nuestro gusto. Dando como resultado, el siguiente logotipo de aplicación para móviles.\par

                \begin{figure} [H]
                    \centering
                    
                    \caption{Icono de la aplicación que se ve al descargarla}
                    \label{fig:a21}
                \end{figure}
                
                Para que cualquier persona pueda descargar la aplicación en su dispositivo móvil, Android Studio también nos permite generar un archivo \textbf{\textit{.apk}}, el cual, es un archivo ejecutable que contiene la aplicación. Al abrir el archivo \textit{\textbf{apk}}, podrá instalar la aplicación en su dispositivo móvil.\par

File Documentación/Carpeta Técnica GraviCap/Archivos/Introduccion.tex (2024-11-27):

\chapter{Introducción}
    
        \section{\textcolor{dark_violet}{\textbf{GraviCap}}, ¿Qué es?}
            \textcolor{dark_violet}{\textbf{GraviCap}} consiste en un condensador de energía gravitatoria junto a un sistema de control de consumo.\par
            Un condensador de energía gravitatoria, o batería de gravedad es una estructura que eleva una carga consumiendo energía eléctrica, para luego almacenarla en forma de energía potencial gravitatoria. El sistema de control de consumo, revisa constantemente el consumo de energía de la red, eligiendo el momento indicado para soltar la carga, que generará la energía cinética que, luego, será transformada en energía eléctrica por un generador.\par
            \textcolor{dark_violet}{\textbf{GraviCap}}, es un prototipo que ha llevado mucho esfuerzo. Desde sus inicios con una ardua investigación hasta su construcción. Este esfuerzo no se limita solo a la construcción de un prototipo, sino que \textcolor{dark_violet}{\textbf{GraviCap}} busca generar un impacto significativo en la forma en que almacenamos energía a nivel mundial. Tal como se detalla en Alcances (\ref{Alc}), \textcolor{dark_violet}{\textbf{GraviCap}} no solo tiene el \textbf{potencial de transformar el almacenamiento de energía} en Argentina, aprovechando las condiciones geográficas favorables del país, sino también de posicionar a nuestro proyecto como una referencia en el ámbito internacional. Al adoptar un enfoque innovador y sostenible, creemos que \textcolor{dark_violet}{\textbf{GraviCap}} puede desempeñar un papel clave en la transición hacia un futuro energético más limpio y eficiente.\par

        \section{Alcances}
        \label{Alc}
            \subsection{Impacto en Argentina}
                La Argentina posee condciones geográficas muy favorables para la implementación de \textbf{energías renovables}, como la solar y la eólica, en las que \textcolor{dark_violet}{\textbf{GraviCap}} podría ser utilizado para expandir las capacidades del suministro energético argentino.\par
                Por ejemplo, \textcolor{dark_violet}{\textbf{GraviCap}} se podría aprovechar  en zonas como:\par
                \begin{itemize} [label=•]
                    \setlength{\itemindent}{1.5em}
                    
                    \item \textbf{Cordillera de los Andes}: La región montañosa de los Andes es ideal para la instalación de baterías gravitatorias debido a su topografía pronunciada y grandes diferencias de altitud. El uso de sistemas como \textcolor{dark_violet}{\textbf{GraviCap}} en esta zona permitiría almacenar energía de manera eficiente, utilizando el desnivel natural de las montañas.\par
                    \item \textbf{Región Patagónica}: La Patagonia, conocida por sus fuertes vientos, es un punto clave para la generación de energía eólica. La instalación de \textcolor{dark_violet}{\textbf{GraviCap}} en esta región permitiría almacenar la energía producida durante los picos de viento, asegurando un suministro constante, incluso en momentos de baja producción.\par
                    \item \textbf{Noroeste Argentino}: Esta región combina un alto potencial solar y una topografía favorable con cerros y mesetas, lo que la convierte en un lugar ideal para la combinación de energía solar y almacenamiento gravitatorio. En zonas como Jujuy y Salta, la alta irradiación solar podría generar electricidad durante el día, que luego sería almacenada por \textcolor{dark_violet}{\textbf{GraviCap}} para su uso durante la noche o en días nublados.\par
                    \item \textbf{Cuyo}: Las provincias de San Juan y Mendoza, además de tener un alto potencial para la energía solar, también cuentan con relieves montañosos que permiten una fácil implementación de \textcolor{dark_violet}{\textbf{GraviCap}}. La combinación de ambos factores ofrecería una solución integrada para el almacenamiento y el aprovechamiento de energía renovable, mejorando la autosuficiencia energética de la región.\par
                \end{itemize}
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

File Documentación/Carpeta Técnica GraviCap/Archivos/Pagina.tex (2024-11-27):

\chapter{Página Web}
    
    \section{Introducción}
    
        La página web desarrollada para \textcolor{dark_violet}{\textbf{GraviCap}} juega un papel fundamental en la difusión y comunicación del proyecto. Su creación responde a la necesidad de tener una plataforma en línea donde se pueda acceder fácilmente a toda la información relevante sobre el proyecto, sus objetivos, sus integrantes y las fases de desarrollo. Este sitio web no solo sirve como un medio de promoción, sino que también actúa como un canal interactivo entre el equipo y el público interesado.\par
        A lo largo del desarrollo del proyecto, consideramos esencial contar con una herramienta que fuera accesible para cualquier persona interesada en conocer más sobre \textcolor{dark_violet}{\textbf{GraviCap}}. Por ello, el sitio web se construyó con un diseño intuitivo y funcional, con el objetivo de proporcionar información clara y precisa, así como facilitar la interacción directa con los visitantes a través de un formulario de contacto. Asimismo, la página está pensada para ser compatible con dispositivos móviles y de escritorio, asegurando que cualquier usuario pueda acceder a la información sin inconvenientes, independientemente del dispositivo que utilice.\par
        Este capítulo describe en detalle el propósito de la página web, su estructura técnica, los componentes que la componen y el proceso seguido para su implementación. Desde la creación de los componentes en Vue.js hasta su despliegue final utilizando Vercel.app, se documentan los pasos clave y las decisiones técnicas que permitieron la construcción de un sitio web eficiente y profesional para el proyecto \textcolor{dark_violet}{\textbf{GraviCap}}.\par
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

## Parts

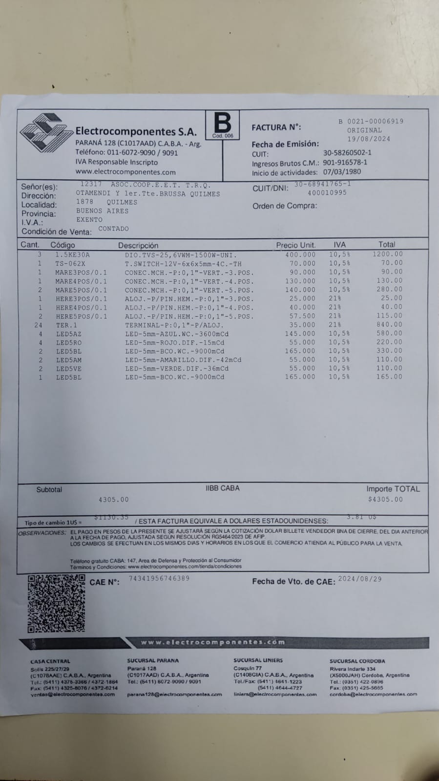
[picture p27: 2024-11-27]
Documentación/Compras/factura_13_ElectrocomponentesSA.jpeg

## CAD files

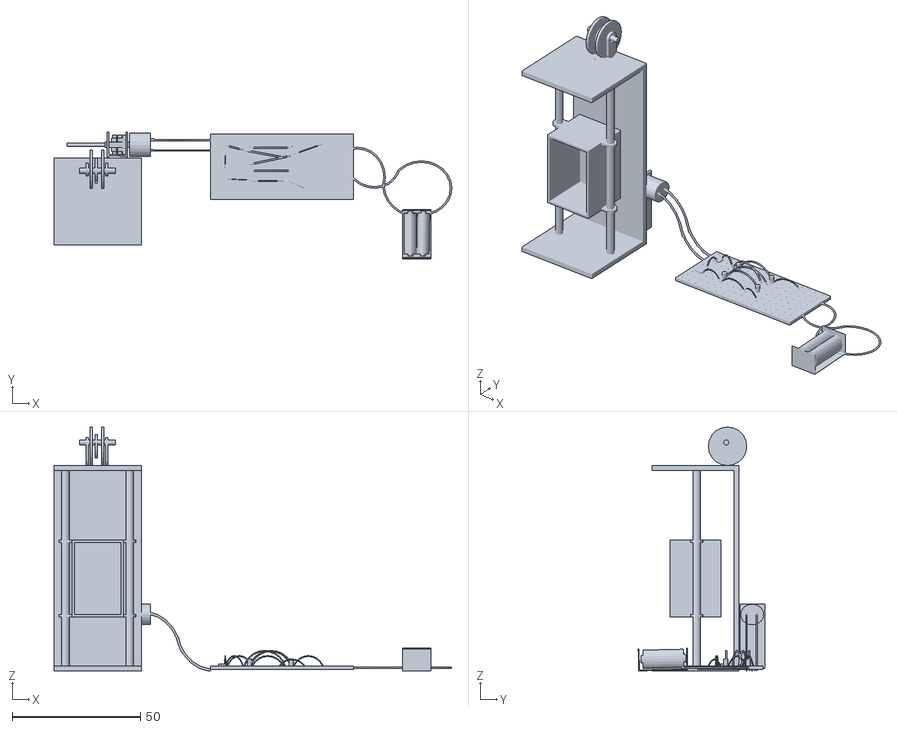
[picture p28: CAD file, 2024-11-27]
Estructura/ejemplo de elevación.stl
155.0 x 49.3 x 95.0

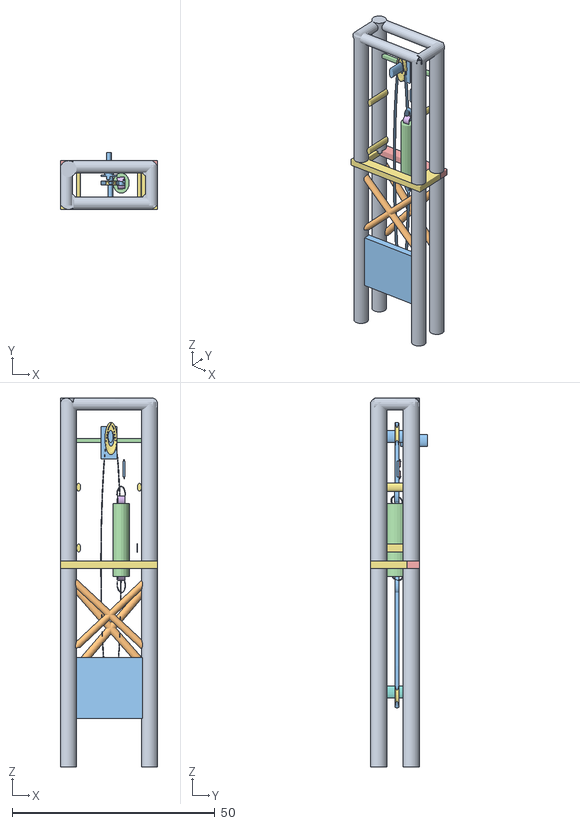
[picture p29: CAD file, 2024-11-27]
Estructura/tinker.obj
24.0 x 14.0 x 91.0

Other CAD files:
Estructura/Gravicap v3 a escala v1.f3d

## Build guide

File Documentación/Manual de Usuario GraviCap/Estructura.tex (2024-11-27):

\chapter{Estructura}
    \section{Materiales}
        \begin{itemize} [label=•]
        \setlength{\itemindent}{3em}
            \item 3 varas de 87 cm de largo y 8 milímetros de grosor.
            \item 1 vara en forma L de 82 cm de largo y 3 milímetros de grosor.
            \item 2 caños de 230 cm de largo y 7,5 cm de ancho. 
            \item 2 estructuras de caños de 98 cm de largo y 89 cm de alto. La superior tiene una polea y la estructura inferior tiene dos poleas.
            \item Placa MPPT.
            \item Placa del microcontrolador del MPPT.
            \item Placa step down.
            \item Placa etapa de control.
            \item Fuente de energía renovable (para este prototipo es un panel solar de 24 voltios).
            \item 6 metros de cable de acero sin recubrimiento de 6 milímetros de grosor.
            \item 1 peso de 30 kilogramos de cemento.
            \item 1 motor.
            \item 1 encoder.
        \end{itemize}
        
    \section{Herramientas}
        \begin{itemize} [label=•]
        \setlength{\itemindent}{3em}
            \item Llave Alem de 6mm.
            \item Llave de 17mm.
            \item Llave de 8mm.
            \item Soportes para el peso.
        \end{itemize}

    \section{Precauciones} 
        Al manipular o mover el peso de la batería se recomienda moverlo entre 2 personas para llevarlo más fácilmente, sugerimos la utilización de calzado de seguridad, guantes y un equipo adecuado para movilizarlo, como una carretilla o carro. Se debe manejar con cuidado para evitar la caída del peso, este puede causar lesiones en personas circundantes o los pisos.\par
        Asegurarse de que la energía generada por la batería sea adecuada para el dispositivo que requiera cargar, para evitar una posible sobrecarga en el dispositivo conectado, quemando o dañando los componentes que lo conforman.\par
        Verificar los valores de voltaje y/o corriente de forma periódica para estar al tanto de cambios repentinos o paulatinos en el funcionamiento del dispositivo.\par
        No realizar mantenimiento en la estructura mientras el cable esté colocado con el peso acoplado.
        Verificar que el cable de acero esté tensado de manera correcta y bien acoplado en el sistema de poleas.\par
        Al armar y desarmar la estructura se debe preveer un soporte para el peso, apoyándolo suavemente por medio de una descarga mientras le quita tensión al cable.\par

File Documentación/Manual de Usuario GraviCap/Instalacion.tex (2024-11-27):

\chapter{Instalación}
    \section{Armado} 
        Este prototipo cuenta con un panel solar como medio de obtención de energía renovable, pero podría utilizarse cualquier otro tipo de generador de energía.\par
        Para evitar atenciones agravadas por la distancia recorrida a través de los cables de conexión, recomendamos colocar la batería cerca del panel solar, u otros, preferentemente en un ambiente cerrado o protegido de la intemperie.\par
        Luego de elegir un espacio protegido de la humedad u otros factores climáticos, alejado de zonas de tránsito recurrente, o habituadas por niños y animales, quitar el embalaje de todas las piezas y prepararlas para su posterior uso.\par
        Recomendamos observar continuamente la foto del dispositivo armado para chequear la posición de cada pieza.\par
        Al ajustar cada bulón, hace falta utilizar una llave de 17mm, y una llave álem de 6mm por el otro lado.\par
        Recomendamos contar con un juego de llaves criquet para facilitar el proceso. Ambas llaves colocadas en simultáneo, con la rosca preparada para un ajuste.\par
        Tener en cuenta, que luego de algunos armados y desarmados las roscas de los bulones y las tuercas pueden verse deterioradas, es importante observar particularmente este punto antes de cada instalación, y reemplazar las piezas en caso de ser necesario. Recomendamos reemplazar en su totalidad los 12 pares de bulón-tuerca cuando uno de ellos aparezca deteriorado.\par
        A continuación, los pasos a seguir:\par

        \begin{enumerate}
            \item Colocar la estructura inferior sobre el suelo.
            \item Tomar uno de los caños de 230cm, y posicionarlo en su lugar.
            \item Ajustar el bulón y la tuerca correspondiente a dicha unión.
            \item Tomar una vara de 87cm de largo, presentarla a modo de escuadra o soporte entre la estructura inferior y el caño vertical, colocado del lado externo a la estructura.
            \item Tomar el caño de 230cm restante y repetir los pasos 2, 3 y 4.
            \item Colocar los dos soportes o escuadras restantes, ajustando únicamente la parte inferior, la pieza quedará haciendo péndulo sobre el caño vertical.
            \item El paso que sigue es posicionar la estructura superior, para esto será necesaria la ayuda de otra persona, esta se quedará sosteniendo la estructura desde el frente, mientras la otra persona ajusta ambos lados de la pieza.
            \item Luego habrá que terminar de colocar los dos soportes colocados en el paso 6, la persona que se encuentra sosteniendo la estructura no podrá soltarla hasta que uno de los dos soportes esté ajustado totalmente.
        \end{enumerate}
        
        La estructura se encuentra armada, ahora hay que colocar el peso y la carga:\par

        \begin{enumerate}
            \item Presentar el motor del dispositivo sobre su respectivo soporte. Ajustar parcialmente la abrazadera a su alrededor.
            \item Tomar las dos varillas roscadas de 5 cm con sus respectivas tuercas y arandelas, ajustando ambas para que mantengan el motor en posición.
            \item Una vez ajustados los soportes, terminar de ajustar la abrazadera, el motor debe estar fijo en su posición.
            \item Tomar el encoder y asegurarlo a la polea adherida al motor. Dejar a disposición sus terminales para su posterior conexión.
            \item Colocar sobre el suelo, debajo de la estructura el banco de soporte previamente seleccionado para sostener el peso.
            \item Trasladar con ayuda de otra persona el mismo hasta posicionarlo sobre dicho banco. Es importante observar que el cable se encuentre adherido al peso por la parte inferior del mismo.
            \item Colocar el cable en los rieles de las 4 poleas.
            \item Asegurando que el ojo de gancho esté lo más abierto posible, colocar el acople 1 entre el peso y la punta del ojo de gancho que no está adherida al cable.
            \item Una vez colocado, cerrar el ojo de gancho lo máximo posible, asegurándose de no girar sobre sí mismo el cable. Recomendamos el uso de una varilla a modo de palanca.
        \end{enumerate}
        
        El dispositivo está armado, resta conectar el panel solar al sistema, el encoder y los terminales del motor.\par
        Asegurarse de que el panel solar se encuentre posicionado y con sus dos terminales disponibles para su conexión. Es importante que en ningún momento se toquen los terminales para evitar dañar el dispositivo.\par
        
        Finalmente:\par

        \begin{enumerate}
            \item Conectar los terminales del encoder a sus respectivas borneras, teniendo en cuenta:

            \begin{itemize} [label=-]
                \item Pin A: Verde
                \item Pin B: Blanco
                \item VCC: Rojo
                \item GND: Negro
                \item Malla de recubrimiento: Malla metálica
            \end{itemize}

            \begin{figure} [H]
                \centering
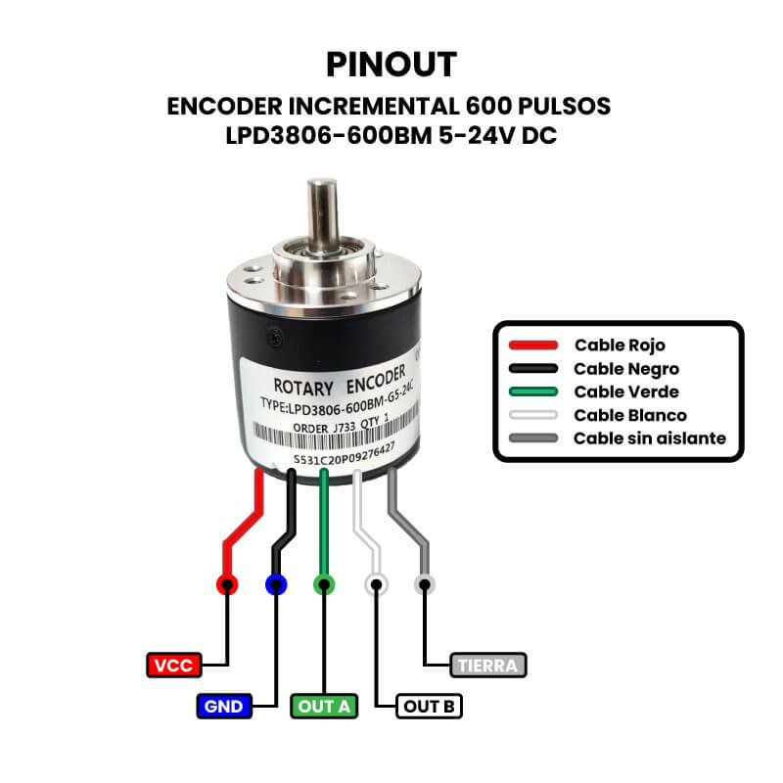
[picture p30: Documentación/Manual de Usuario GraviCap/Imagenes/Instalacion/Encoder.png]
                
            \end{figure}
            
            \item Conectar los terminales del motor a sus respectivas borneras.
            \item Conectar los terminales del panel solar a sus respectivas borneras.

        \end{enumerate}

        \begin{figure}
            \centering
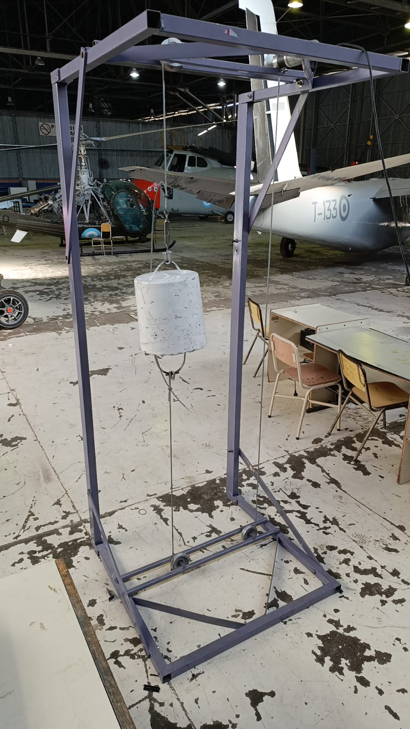
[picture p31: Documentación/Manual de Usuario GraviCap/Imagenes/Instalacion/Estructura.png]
            
        \end{figure}

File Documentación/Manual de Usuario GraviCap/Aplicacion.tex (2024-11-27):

\chapter{Aplicación}
    \section{Requisitos}
        \begin{itemize}
            \item Conexión a WiFi.
            \item Encontrarse cerca de la batería.
            \item Celular Android.
            \item Versión de Android 11 o superior.
            \item Espacio de 10 MB (Megabytes) en su celular.
        \end{itemize}

    \section{Guía de Instalación}
       Para descargar la aplicación en su dispositivo móvil, deberá ingresar desde su celular a nuestro repositorio de github, más concretamente hacia la parte de la app. Puede ir directo hacia allá con el siguiente link:\par
       
       \vspace{0.5cm}
       
       \begin{center}
           \href{https://github.com/impatrq/gravicap/tree/main/GraviCap_app/Instalacion%20de%20la%20Aplicacion%20Movil}{https://github.com/impatrq/gravicap/tree/main/GraviCap\_app/Instalacion\%20de\%20la\%20Aplicacion\%20Movil}\par
       \end{center}

        \vspace{0.5cm}
        
        Una vez ingresemos al link, veremos los siguientes archivos:\par
        
        \begin{figure} [H]
            \centering
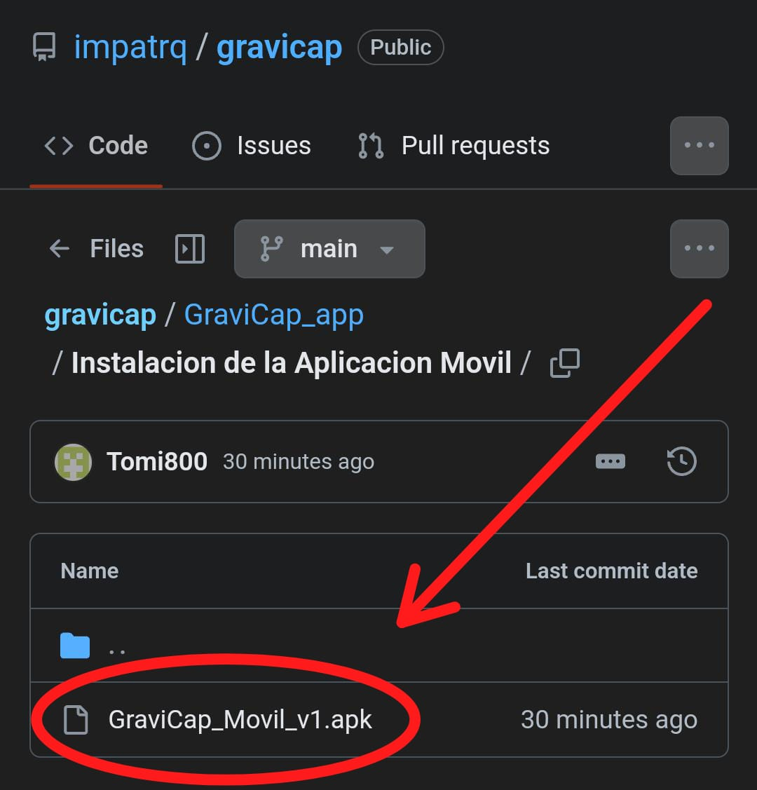
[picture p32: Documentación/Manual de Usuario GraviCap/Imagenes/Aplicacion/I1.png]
            
        \end{figure}
        
        Ingresamos al archivo indicado, el cual es el .apk de la aplicación, el archivo ejecutable para poder descargar la aplicación desde el celular. También podremos encontrar otros archivos .apk, los cuales son las diferentes versiones de la app.\par

        \begin{figure} [H]
            \centering
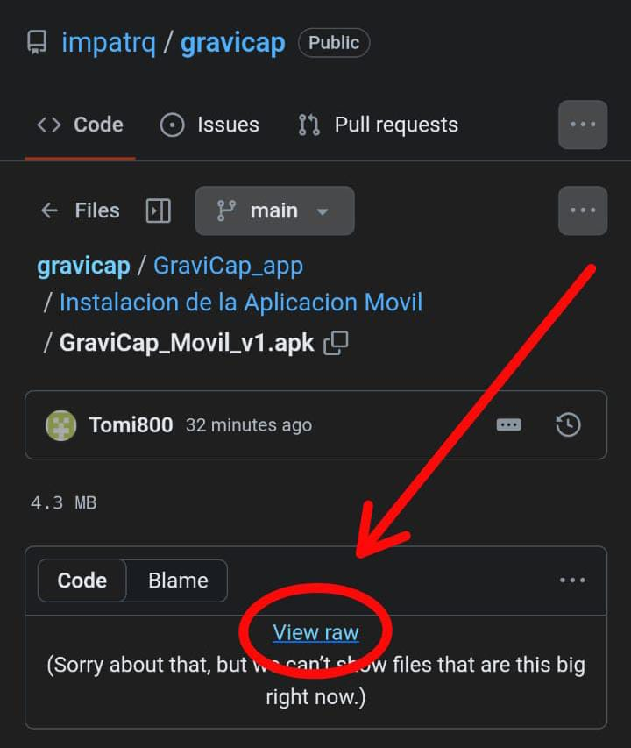
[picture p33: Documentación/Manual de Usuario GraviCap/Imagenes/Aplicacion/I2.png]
            
        \end{figure}

        Presionaremos el botón de “view raw” para descargar la aplicación.\par

        \begin{figure} [H]
            \centering
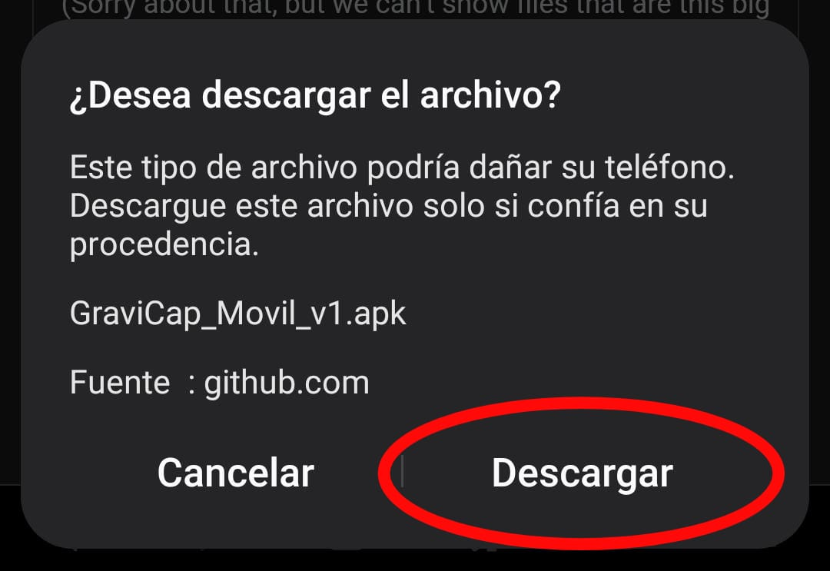
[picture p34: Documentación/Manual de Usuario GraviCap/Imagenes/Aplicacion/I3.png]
            
        \end{figure}

        Finalmente, reconocerá que se quiere descargar la aplicación, solamente presionamos el botón de “descargar” y comenzará la descarga de la aplicación.\par
        También puede que dependiendo de su sistema operativo y celular, requiera de aceptar la descarga nuevamente.\par
        Una vez descargada, podrá ingresar directamente y podrá ver la aplicación en su celular de esta manera.\par

        \begin{figure} [H]
            \centering
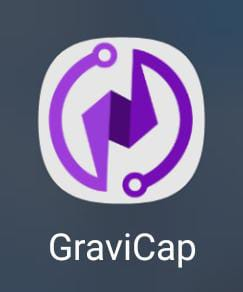
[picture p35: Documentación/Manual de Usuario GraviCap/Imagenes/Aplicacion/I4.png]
            
        \end{figure}
        \begin{center}
            \Large{\textbf{¡Felicidades, ya puede utilizar la aplicación de \textcolor{dark_violet}{GraviCap}!}}\par
        \end{center}
        
        \newpage
    \section{Bienvenida}
        Cada usuario, al ingresar a la aplicación, verá nuestro logo con su respectivo nombre, y slogan.\par

        \begin{figure} [H]
            \centering
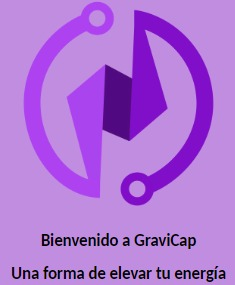
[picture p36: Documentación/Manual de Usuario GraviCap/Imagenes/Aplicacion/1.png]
            
        \end{figure}

        También encontrará un texto que le proveerá una pequeña información de nuestro producto, los valores de la batería que podrá monitorear, así también como gráficos lineales en base a valores registrados de la batería.\par

        \begin{figure} [H]
            \centering
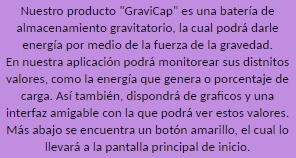
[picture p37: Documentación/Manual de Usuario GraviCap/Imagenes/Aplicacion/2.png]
            
        \end{figure}

        Una vez el usuario haya leído el texto, encontrará en la parte inferior de la pantalla un botón amarillo con texto “Pulse Aquí para ir a Inicio” el cual lo llevará hacia la pantalla de principal de Inicio para poder navegar por las diferentes pantallas y ver los valores de la batería.\par

        \begin{figure} [H]
            \centering
            
        \end{figure}

        \begin{figure} [H]
            \centering
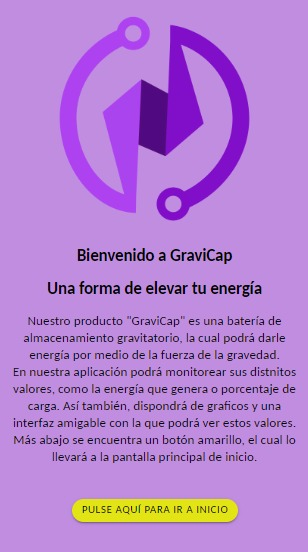
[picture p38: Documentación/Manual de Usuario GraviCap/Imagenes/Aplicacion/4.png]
            
        \end{figure}

    \section{Inicio}
        Al pulsar el botón de la pantalla de bienvenida, se encontrará con la pantalla principal, la pantalla de inicio. Teniendo en cuenta la navegación del usuario por los diferentes valores, situamos los botones pensando en un recorrido eficiente, intuitivo y amigable para el mismo.\par
        La primera parte que verá el usuario, será una barra blanca en la parte superior (header), contando con nuestro logo en la parte izquierda, un texto amigable de bienvenida en la parte central y un botón de información en la parte izquierda, el cual, contiene nuestras redes y contactos.

        \begin{figure} [H]
            \centering
            
        \end{figure}

        \begin{figure} [H]
            \centering
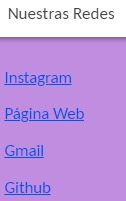
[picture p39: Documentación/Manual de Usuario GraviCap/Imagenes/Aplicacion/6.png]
            
        \end{figure}

        En la parte central de la pantalla, el usuario podrá ver su contenido principal, conformado por botones con imágenes y textos referenciados al valor que podrá monitorear.\par
        Estos están ubicados de forma tal que el usuario pueda ver y entrar a las pantallas de los valores importantes con mayor comodidad.\par
        Los dos botones ubicados en la parte de arriba son los valores más importantes y la sección de los tres botones en la parte inferior no serán de primordial importancia para el usuario. Algunos de estos valores son: la energía que genera la batería; su carga; el consumo que tiene el usuario; los valores del panel solar y valores generales de la batería.\par

        \begin{figure} [H]
            \centering
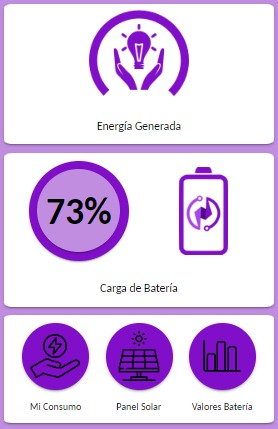
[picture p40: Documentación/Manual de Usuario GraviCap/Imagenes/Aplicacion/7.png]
            
        \end{figure}

        En la parte inferior izquierda encontraremos un pequeño botón amarillo con texto “Página de Gráficos” el cual, nos enviará a una pantalla en la cual podremos ver los distnitos tipos de gráficos de potencia de la batería.\par

        \begin{figure} [H]
            \centering
            
        \end{figure}

        \begin{figure} [H]
            \centering
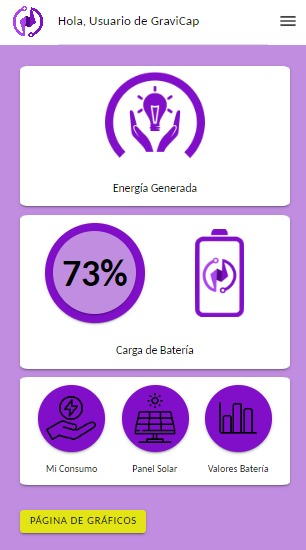
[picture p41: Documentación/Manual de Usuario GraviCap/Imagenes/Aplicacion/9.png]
            
        \end{figure}

    \section{Paginas y Valores}
        Todas las pantallas cuentan con una barra blanca (header) en la parte superior que contienen un botón para ir hacia atrás, es decir, que podrán volver a la pantalla principal de inicio.\par
        Una de las pantallas importantes que podrá ver el usuario es la de “Energía Generada”. El usuario, al entrar, verá un gráfico circular con el valor de potencia que tiene la batería. En la parte inferior podrán ver un texto referenciando el color del gráfico y el valor plasmado en la pantalla.\par

        \begin{figure} [H]
            \centering
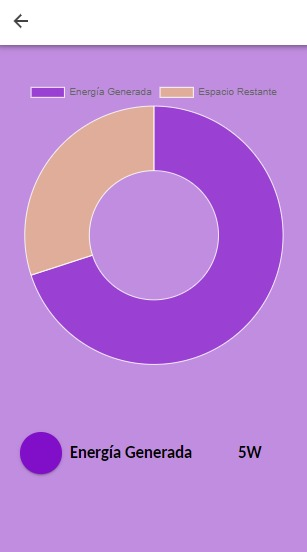
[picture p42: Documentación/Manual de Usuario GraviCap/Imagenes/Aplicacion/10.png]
            
        \end{figure}

        El usuario contará con la pantalla de “Carga de Batería” en la cual podrá ver un circulo de color violeta con un valor de carga porcentual, referenciando la carga que tiene la batería en ese momento, siendo el 100\% cuando el peso está en su punto más alto y el 0\% cuando el peso está en su punto más bajo. En la parte inferior el usuario podrá ver el tiempo que le falta a la batería para completar su carga.\par

        \begin{figure} [H]
            \centering
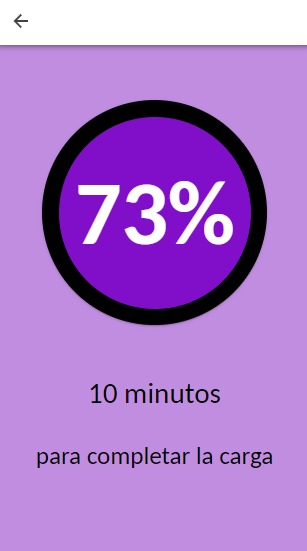
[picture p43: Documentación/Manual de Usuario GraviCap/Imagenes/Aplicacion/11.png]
            
        \end{figure}
        
        En la sección ubicada en la parte inferior podremos encontrar tres botones violetas con imágenes, referenciados a las pantallas de: consumo del usuario, valores del panel solar, valores generales de la batería.\par

        \begin{figure} [H]
            \centering
            
        \end{figure}

        El usuario tendrá una pantalla dedicada para saber el consumo del dispositivo que esté cargando, esta pantalla será “Mi consumo”, esta pantalla contendrá una imagen de referencia del botón visto anteriormente y una carta con el texto “Su consumo es:” y el valor de potencia en watts.\par

        \begin{figure} [H]
            \centering
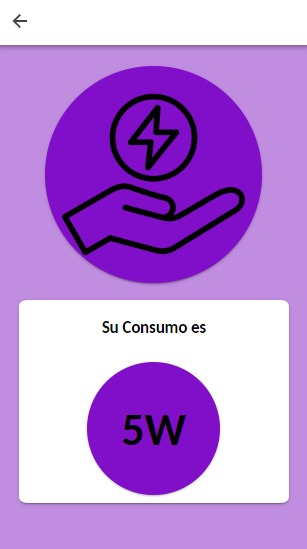
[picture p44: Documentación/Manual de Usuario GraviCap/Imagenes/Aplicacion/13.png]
            
        \end{figure}

        Para poder saber los valores del panel solar, el usuario dispone de la pantalla de “Panel Solar” en la cual podrá ver un circulo morado con una imagen de referencia del botón visto anteriormente y una carta con el texto “Valores del Panel Solar” y dos apartados: uno del voltaje con su respectivo valor en volts y el otro apartado de potencia con su respectivo valor en watts.\par

        \begin{figure} [H]
            \centering
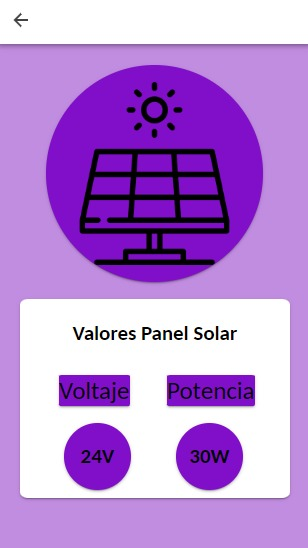
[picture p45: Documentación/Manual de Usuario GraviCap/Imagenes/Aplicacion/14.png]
            
        \end{figure}

        El último botón de la sección de tres le provee al usuario una información general de los “Valores de Batería”. Al ingresar en esta pantalla, el usuario verá un gráfico de tipo columnas referenciando 3 valores de la batería: voltaje, amperaje y wataje (potencia). En la parte inferior se podrá encontrar los valores numéricos de cada uno, referenciados con un círculo violeta y letras blancas.\par

        \begin{figure} [H]
            \centering
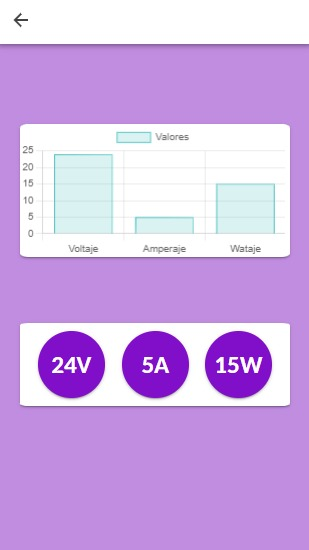
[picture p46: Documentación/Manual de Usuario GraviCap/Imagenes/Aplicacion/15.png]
            
        \end{figure}

    \section{Gráficos}
        Como se mencionó anteriormente, en la parte de la pantalla de inicio hay un botón que lleva al usuario a la pantalla de “Gráficos de la Batería”. Esta sección está creada para que el usuario pueda ver el funcionamiento de la batería en el momento de ascenso y descenso del peso, referenciado con valores de potencia en función del tiempo. El usuario, al entrar, verá una carta blanca con una imagen de gráfico con dos líneas, referenciando a los dos gráficos de potencia que podrá ver el usuario.\par

        \begin{figure} [H]
            \centering
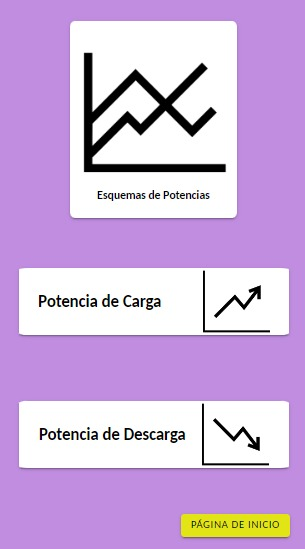
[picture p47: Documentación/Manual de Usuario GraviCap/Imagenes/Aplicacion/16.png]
            
        \end{figure}
        
        La parte central contiene dos botones, uno, el más de más arriba, con el texto “Potencia de Carga” con una imagen de un gráfico de línea ascendente.\par

        \begin{figure} [H]
            \centering
            
        \end{figure}

        El botón de más abajo contiene el texto “Potencia de Descarga” con un gráfico de línea descendente.\par

        \begin{figure} [H]
            \centering
            
        \end{figure}

        En la parte inferior de la página de gráficos el usuario verá un botón pequeño amarillo del mismo etilo que el de la pantalla de inicio, con el texto de “Página de Inicio” que al presionarlo lo llevará devuelta hacia la pantalla de inicio principal. \par

        \begin{figure} [H]
            \centering
            
        \end{figure}

        Al presionar el botón con el icono de gráfico ascendente, el usuario podrá ver la pantalla de Potencia de Carga, esta es muy simple, únicamente encontrará el gráfico de línea ascendente de la batería, este se basa en la potencia que tiene la batería en el lapso de tiempo que este asciende, creando así un gráfico de potencia en función del tiempo.\par
        También, en la parte superior izquierda, encontramos un botón para volver atrás a la página de gráficos.\par

        \begin{figure} [H]
            \centering
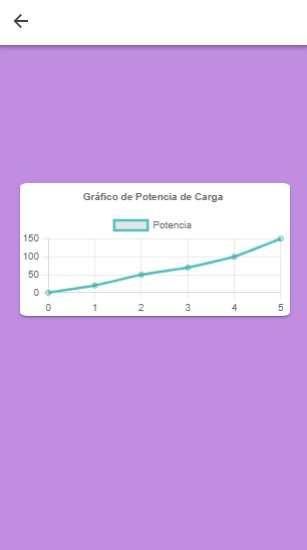
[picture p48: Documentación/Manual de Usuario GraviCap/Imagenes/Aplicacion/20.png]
            
        \end{figure}

        El segundo botón que contiene el icono de un gráfico descendente encontramos en la página de gráficos es el botón de Potencia de Descarga. Este actúa de igual forma que el botón mencionado anteriormente, únicamente que éste nos marcará el gráfico de potencia en función del tiempo cuando el peso esté en su momento de descenso.\par
        Este también cuenta con el botón para volver hacia atrás a la página de gráficos.\par

        \begin{figure} [H]
            \centering
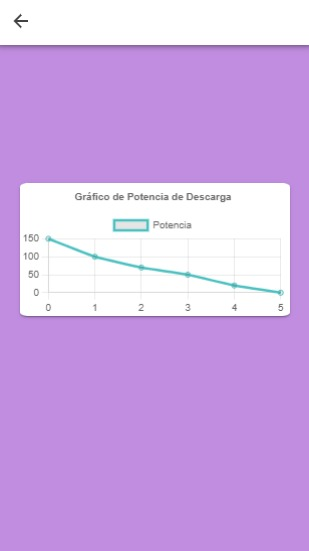
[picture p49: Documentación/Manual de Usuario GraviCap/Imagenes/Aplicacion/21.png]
            
        \end{figure}

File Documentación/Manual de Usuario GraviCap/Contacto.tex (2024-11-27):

\chapter{Contacto}

    \textbf{Link a la web:}
    \href{https://gravicap.vercel.app}{https://gravicap.vercel.app} 
    
    \textbf{Link a trello:}
    \href{https://trello.com/b/EtjuqFFQ/kanban}{https://trello.com/b/EtjuqFFQ/kanban}
    
    \textbf{Link a github:}
    \href{https://github.com/impatrq/gravicap}{https://github.com/impatrq/gravicap}
    
    \textbf{Link redes sociales:}
    \href{https://www.instagram.com/gravi.cap/}{https://www.instagram.com/gravi.cap/}

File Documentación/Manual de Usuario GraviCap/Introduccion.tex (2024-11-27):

\chapter{Introducción}
    \section{¿Qué es \textcolor{dark_violet}{GraviCap}?}
        \textcolor{dark_violet}{GraviCap} (Gravity Capacitor) es una batería de almacenamiento gravitatorio. Su finalidad es igual a una batería convencional, pero con un funcionamiento de generación de energía totalmente distinto e innovador.\par

    \section{Funcionamiento Principal}
        Esta batería está conformada por una estructura, la cual eleva un peso por medio de un motor, un sistema de poleas y un cable de acero, almacenando energía potencial gravitatoria en el peso. Cuando se necesita energía en el dispositivo que queramos cargar, el motor hará descender la masa de manera controlada, generando energía eléctrica gracias al movimiento del motor al ser movido por el cable.\par

    \section{Objetivos}
        Teniendo en cuenta como fenómeno mundial, la contaminación por baterías convencionales, ya sea de litio, de autos o de celulares, surge nuestro objetivo principal, darle al mundo una nueva alternativa de almacenamiento de energía por medio de nuestro producto, trayendo a nuestro país una nueva forma de batería, siendo ideal para usarla con energías renovables, no contaminantes y sustentables. Finalmente presentando al mundo una forma sustentable y no contaminante de almacenar energía.\par
        
    \section{Beneficios}
        \begin{itemize}
            \item Nuestra batería, al tener como factor principal aprovechar la energía potencial gravitatoria para la generación de energía eléctrica, es completamente sustentable y no contaminante para el medio ambiente.\par
            \item Esta forma de generación de energía es poco vista e implementada dentro del mundo y de las primeras utilizadas en Argentina. Siendo así, una nueva forma vanguardista de batería dentro de nuestro país.
            \item Puede aprovecharse lugares o infraestructuras en desuso para la instalación de la batería. Por ejemplo, minas abandonadas, contando con una gran profundidad para el recorrido del peso. También, puede aprovecharse una torre de control de un aeródromo o aeropuerto, contando con una gran altura para un eficiente funcionamiento y recorrido del peso. 
            \item El sistema de almacenamiento de energía sobrante de las fuentes utilizadas, garantiza para el usuario una estabilidad de energía en la batería en los momentos de pico o baja consumo aprovechando al máximo lo que genera.
            \item Gracias al sistema mecánico de \textcolor{dark_violet}{GraviCap} se producen menos desgastes en la estructura en la carga y descarga de energía, así proporcionando una vida útil más larga que una batería convencional y, por ende, menos coste de mantenimiento. 
            \item Permite monitorear el funcionamiento del sistema \textcolor{dark_violet}{GraviCap} por medio de una aplicación móvil.
        
        \end{itemize}

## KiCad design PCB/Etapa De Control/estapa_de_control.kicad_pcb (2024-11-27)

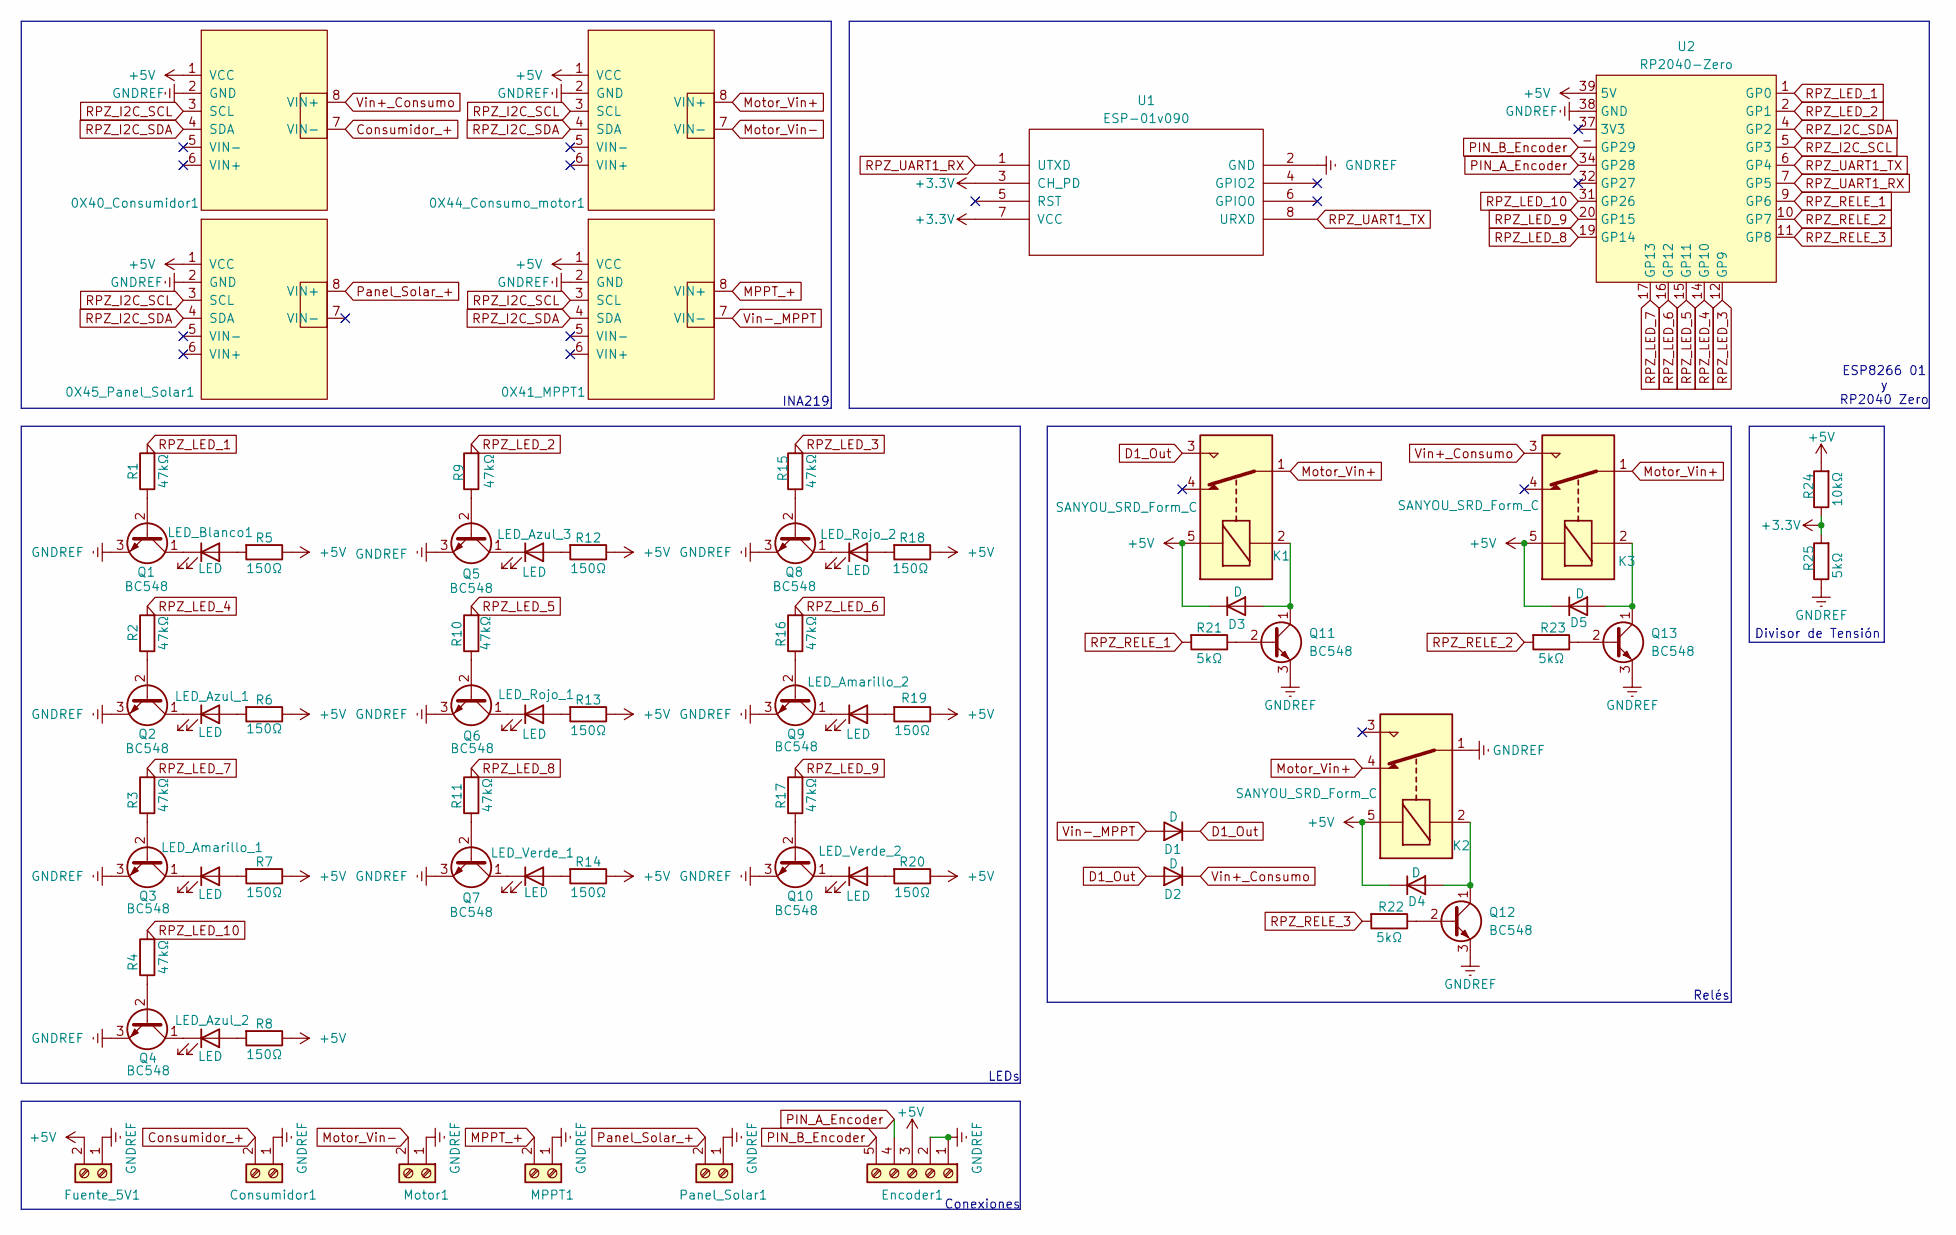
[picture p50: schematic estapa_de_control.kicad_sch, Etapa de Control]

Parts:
0X40_Consumidor1, 0X41_MPPT1, 0X44_Consumo_motor1, 0X45_Panel_Solar1: module_ina219
Consumidor1: Screw_Terminal_01x02; TerminalBlock_bornier-2_P5.08mm
D1, D2, D3, D4, D5: D; D_5W_P10.16mm_Horizontal
Encoder1: Screw_Terminal_01x05; TerminalBlock_bornier-5_P5.08mm
Fuente_5V1: Screw_Terminal_01x02; TerminalBlock_bornier-2_P5.08mm
K1, K2, K3: SANYOU_SRD_Form_C; Relay_SPDT_SANYOU_SRD_Series_Form_C
LED_Amarillo_1, LED_Amarillo_2: LED; LED_D3.0mm
LED_Azul_1, LED_Azul_2, LED_Azul_3: LED; LED_D3.0mm
LED_Blanco1: LED; LED_D3.0mm
LED_Rojo_1, LED_Rojo_2: LED; LED_D3.0mm
LED_Verde_1, LED_Verde_2: LED; LED_D3.0mm
MPPT1: Screw_Terminal_01x02; TerminalBlock_bornier-2_P5.08mm
Motor1: Screw_Terminal_01x02; TerminalBlock_bornier-2_P5.08mm
Panel_Solar1: Screw_Terminal_01x02; TerminalBlock_bornier-2_P5.08mm
Q1, Q2, Q3, Q4, Q5, Q6, Q7, Q8, Q9, Q10, Q11, Q12, Q13: BC548; TO-92_Inline
R1, R2, R3, R4, R9, R10, R11, R15, R16, R17: 47kΩ; R_Axial_DIN0204_L3.6mm_D1.6mm_P7.62mm_Horizontal
R5, R6, R7, R8, R12, R13, R14, R18, R19, R20: 150Ω; R_Axial_DIN0204_L3.6mm_D1.6mm_P7.62mm_Horizontal
R21, R22, R23, R25: 5kΩ; R_Axial_DIN0204_L3.6mm_D1.6mm_P7.62mm_Horizontal
R24: 10kΩ; R_Axial_DIN0204_L3.6mm_D1.6mm_P7.62mm_Horizontal
U1: ESP-01v090; ESP-01
U2: RP2040-Zero; RP2040 Zero

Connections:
+3.3V: R24.1, R25.2, U1.3 (CH_PD), U1.7 (VCC)
+5V: 0X40_Consumidor1.1 (VCC), 0X41_MPPT1.1 (VCC), 0X44_Consumo_motor1.1 (VCC), 0X45_Panel_Solar1.1 (VCC), D3.1 (K), D4.1 (K), D5.1 (K), Encoder1.3, Fuente_5V1.2, K1.5, K2.5, K3.5, R5.1, R6.1, R7.1, R8.1, R12.1, R13.1, R14.1, R18.1, R19.1, R20.1, R24.2, U2.39 (5V)
Consumidor_+: 0X40_Consumidor1.7 (VIN-), Consumidor1.2
D1_Out: D1.1 (K), D2.2 (A), K1.3
GNDREF: 0X40_Consumidor1.2 (GND), 0X41_MPPT1.2 (GND), 0X44_Consumo_motor1.2 (GND), 0X45_Panel_Solar1.2 (GND), Consumidor1.1, Encoder1.1, Encoder1.2, Fuente_5V1.1, K2.1, MPPT1.1, Motor1.1, Panel_Solar1.1, Q1.3 (E), Q2.3 (E), Q3.3 (E), Q4.3 (E), Q5.3 (E), Q6.3 (E), Q7.3 (E), Q8.3 (E), Q9.3 (E), Q10.3 (E), Q11.3 (E), Q12.3 (E), Q13.3 (E), R25.1, U1.2 (GND), U2.38 (GND)
MPPT_+: 0X41_MPPT1.8 (VIN+), MPPT1.2
Motor_Vin+: 0X44_Consumo_motor1.8 (VIN+), K1.1, K2.4, K3.1
Motor_Vin-: 0X44_Consumo_motor1.7 (VIN-), Motor1.2
unnamed: D3.2 (A), K1.2, Q11.1 (C)
unnamed: D4.2 (A), K2.2, Q12.1 (C)
unnamed: D5.2 (A), K3.2, Q13.1 (C)
unnamed: LED_Amarillo_1.2 (A), R7.2
unnamed: LED_Amarillo_1.1 (K), Q3.1 (C)
unnamed: LED_Amarillo_2.2 (A), R19.2
unnamed: LED_Amarillo_2.1 (K), Q9.1 (C)
unnamed: LED_Azul_1.2 (A), R6.2
unnamed: LED_Azul_1.1 (K), Q2.1 (C)
unnamed: LED_Azul_2.2 (A), R8.2
unnamed: LED_Azul_2.1 (K), Q4.1 (C)
unnamed: LED_Azul_3.2 (A), R12.2
unnamed: LED_Azul_3.1 (K), Q5.1 (C)
unnamed: LED_Blanco1.2 (A), R5.2
unnamed: LED_Blanco1.1 (K), Q1.1 (C)
unnamed: LED_Rojo_1.2 (A), R13.2
unnamed: LED_Rojo_1.1 (K), Q6.1 (C)
unnamed: LED_Rojo_2.2 (A), R18.2
unnamed: LED_Rojo_2.1 (K), Q8.1 (C)
unnamed: LED_Verde_1.2 (A), R14.2
unnamed: LED_Verde_1.1 (K), Q7.1 (C)
unnamed: LED_Verde_2.2 (A), R20.2
unnamed: LED_Verde_2.1 (K), Q10.1 (C)
unnamed: Q1.2 (B), R1.1
unnamed: Q2.2 (B), R2.1
unnamed: Q3.2 (B), R3.1
unnamed: Q4.2 (B), R4.1
unnamed: Q5.2 (B), R9.1
unnamed: Q6.2 (B), R10.1
unnamed: Q7.2 (B), R11.1
unnamed: Q8.2 (B), R15.1
unnamed: Q9.2 (B), R16.1
unnamed: Q10.2 (B), R17.1
unnamed: Q11.2 (B), R21.1
unnamed: Q12.2 (B), R22.1
unnamed: Q13.2 (B), R23.1
PIN_A_Encoder: Encoder1.4, U2.34 (GP28)
PIN_B_Encoder: Encoder1.5, U2.- (GP29)
Panel_Solar_+: 0X45_Panel_Solar1.8 (VIN+), Panel_Solar1.2
RPZ_I2C_SCL: 0X40_Consumidor1.3 (SCL), 0X41_MPPT1.3 (SCL), 0X44_Consumo_motor1.3 (SCL), 0X45_Panel_Solar1.3 (SCL), U2.5 (GP3)
RPZ_I2C_SDA: 0X40_Consumidor1.4 (SDA), 0X41_MPPT1.4 (SDA), 0X44_Consumo_motor1.4 (SDA), 0X45_Panel_Solar1.4 (SDA), U2.4 (GP2)
RPZ_LED_1: R1.2, U2.1 (GP0)
RPZ_LED_2: R9.2, U2.2 (GP1)
RPZ_LED_3: R15.2, U2.12 (GP9)
RPZ_LED_4: R2.2, U2.14 (GP10)
RPZ_LED_5: R10.2, U2.15 (GP11)
RPZ_LED_6: R16.2, U2.16 (GP12)
RPZ_LED_7: R3.2, U2.17 (GP13)
RPZ_LED_8: R11.2, U2.19 (GP14)
RPZ_LED_9: R17.2, U2.20 (GP15)
RPZ_LED_10: R4.2, U2.31 (GP26)
RPZ_RELE_1: R21.2, U2.9 (GP6)
RPZ_RELE_2: R23.2, U2.10 (GP7)
RPZ_RELE_3: R22.2, U2.11 (GP8)
RPZ_UART1_RX: U1.1 (UTXD), U2.7 (GP5)
RPZ_UART1_TX: U1.8 (URXD), U2.6 (GP4)
Vin+_Consumo: 0X40_Consumidor1.8 (VIN+), D2.1 (K), K3.3
Vin-_MPPT: 0X41_MPPT1.7 (VIN-), D1.2 (A)

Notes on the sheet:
Relés
INA219
ESP8266 01 y RP2040 Zero
Divisor de Tensión
LEDs
Conexiones

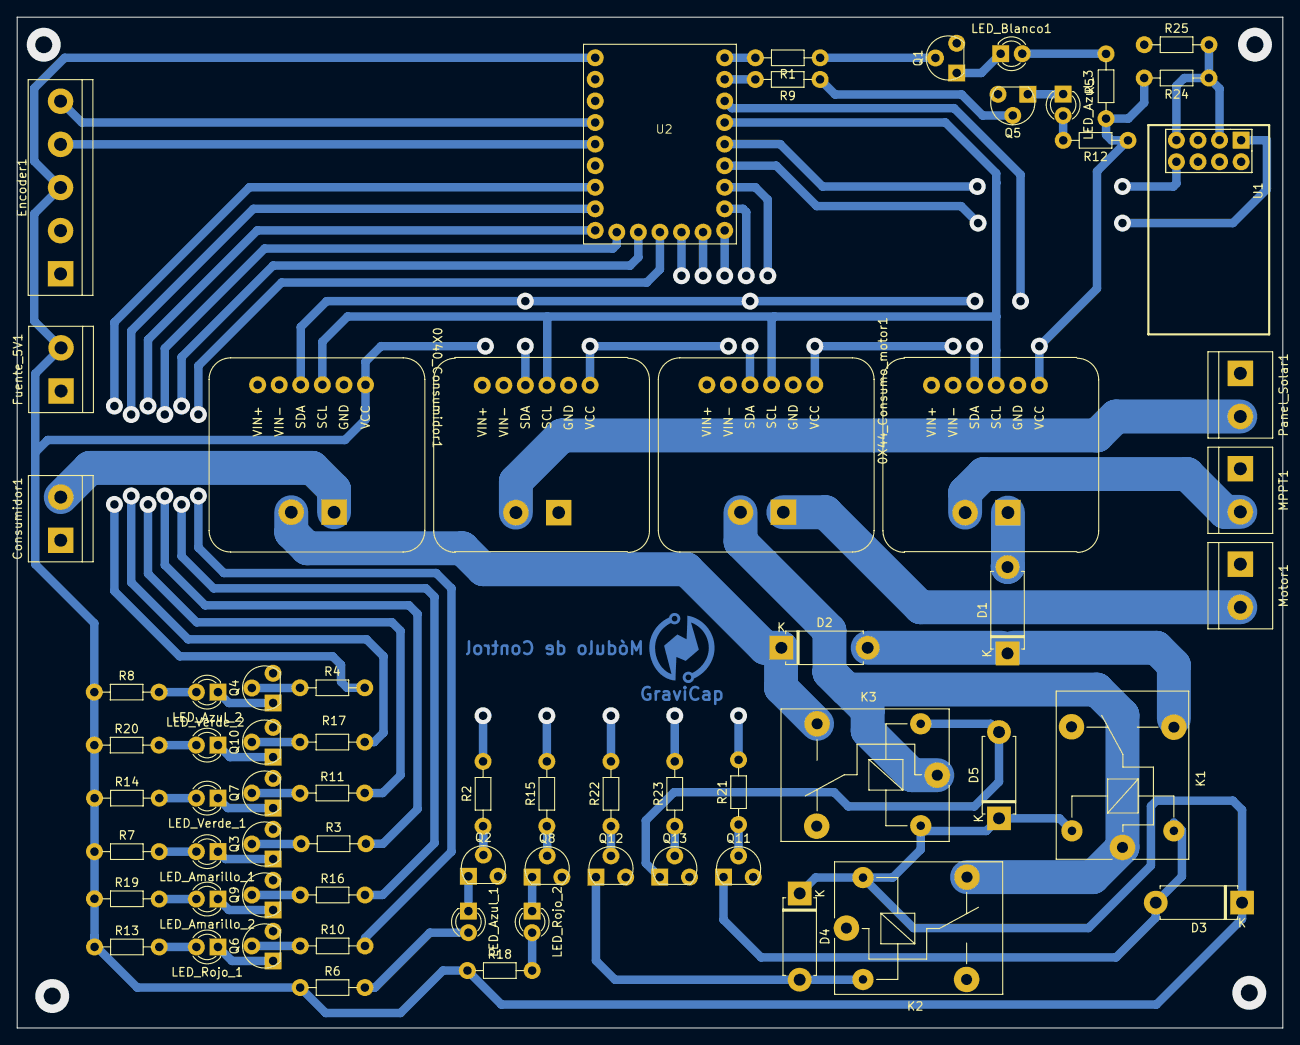
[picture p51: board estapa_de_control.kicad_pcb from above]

Board: 2 copper layers, 149.0 x 119.0 mm, 69 parts (0 on the bottom side), 66 nets.

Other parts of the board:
GraviCap: LOGO

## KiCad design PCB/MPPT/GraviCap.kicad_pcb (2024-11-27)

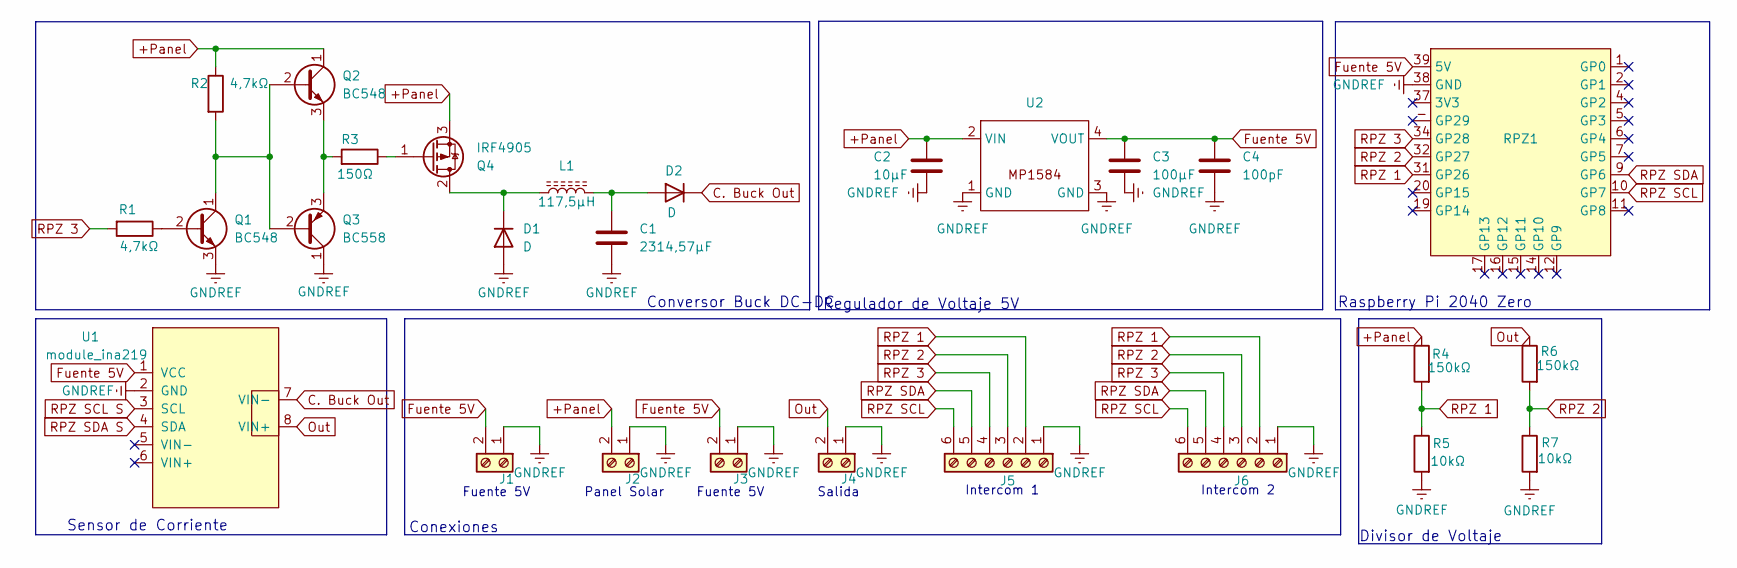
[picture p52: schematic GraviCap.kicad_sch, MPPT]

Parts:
C1: 2314,57µF; CP_Radial_D18.0mm_P7.50mm
C2: 10µF; CP_Radial_D4.0mm_P2.00mm
C3: 100µF; CP_Radial_D6.3mm_P2.50mm
C4: 100pF; C_Disc_D4.3mm_W1.9mm_P5.00mm
D1, D2: D; TO-220-3_Vertical
J1, J2, J3, J4: Screw_Terminal_01x02; TerminalBlock_bornier-2_P5.08mm
J5, J6: Screw_Terminal_01x06; TerminalBlock_bornier-6_P5.08mm
L1: 117,5µH; L_Toroid_Horizontal_D41.9mm_P37.60mm_Vishay_TJ7
Q1, Q2: BC548; TO-92_Inline
Q3: BC558; TO-92_Inline
Q4: IRF4905; TO-220-3_Vertical
R1, R2: 4,7kΩ; R_Axial_DIN0204_L3.6mm_D1.6mm_P7.62mm_Horizontal
R3: 150Ω; R_Axial_DIN0204_L3.6mm_D1.6mm_P7.62mm_Horizontal
R4, R6: 150kΩ; R_Axial_DIN0204_L3.6mm_D1.6mm_P7.62mm_Horizontal
R5, R7: 10kΩ; R_Axial_DIN0204_L3.6mm_D1.6mm_P7.62mm_Horizontal
RPZ1: RP2040 Zero
U1: module_ina219; INA_219
U2: MP1584

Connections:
+Panel: C2.1, J2.2, Q2.1 (C), Q4.3 (S), R2.1, R4.1, U2.2 (VIN); also elsewhere on the board
C. Buck Out: D2.1 (K), U1.7 (VIN-)
Fuente 5V: C3.1, C4.1, J1.2, J3.2, RPZ1.39 (5V), U1.1 (VCC), U2.4 (VOUT)
GNDREF: C1.2, C2.2, C3.2, C4.2, D1.2 (A), J1.1, J2.1, J3.1, J4.1, J5.1, J6.1, Q1.3 (E), Q3.1 (C), R5.2, R7.2, RPZ1.38 (GND), U1.2 (GND), U2.1 (GND), U2.3 (GND)
unnamed: D1.1 (K), L1.1, Q4.2 (D)
unnamed: C1.1, D2.2 (A), L1.2
unnamed: Q1.2 (B), R1.1
unnamed: Q1.1 (C), Q2.2 (B), Q3.2 (B), R2.2
unnamed: Q2.3 (E), Q3.3 (E), R3.2
unnamed: Q4.1 (G), R3.1
Out: J4.2, R6.1, U1.8 (VIN+)
RPZ 1: J5.2, J6.2, R4.2, R5.1, RPZ1.31 (GP26); also elsewhere on the board
RPZ 2: J5.3, J6.3, R6.2, R7.1, RPZ1.32 (GP27)
RPZ 3: J5.4, J6.4, R1.2, RPZ1.34 (GP28)
RPZ SCL: J5.6, J6.6, RPZ1.10 (GP7)
RPZ SCL S: U1.3 (SCL)
RPZ SDA: J5.5, J6.5, RPZ1.9 (GP6)
RPZ SDA S: U1.4 (SDA)

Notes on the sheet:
Conversor Buck DC-DC
Regulador de Voltaje 5V
Raspberry Pi 2040 Zero
Intercom 1
Salida
Fuente 5V
Conexiones
Divisor de Voltaje
Intercom 2
Panel Solar
Sensor de Corriente

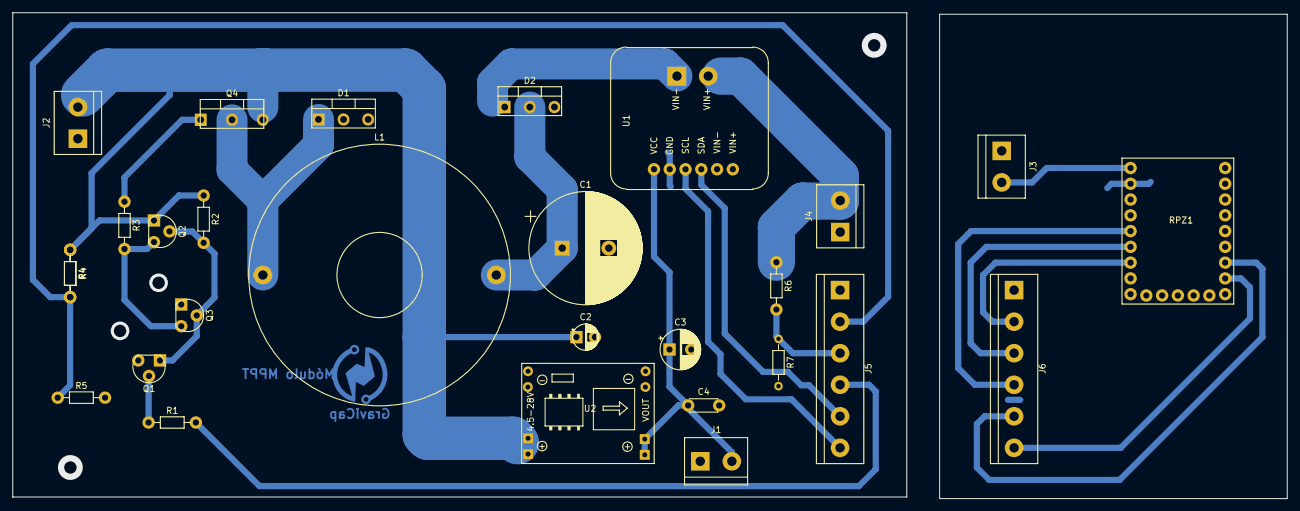
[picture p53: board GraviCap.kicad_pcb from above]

Board: 2 copper layers, 144.0 x 78.0 mm, 29 parts (1 on the bottom side), 16 nets.

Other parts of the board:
GraviCap: GraviCap_Logo
R4#2: 150kΩ; R_Axial_DIN0204_L3.6mm_D1.6mm_P7.62mm_Horizontal

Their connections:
+Panel: R4#2.1; also elsewhere on the board
RPZ 1: R4#2.2; also elsewhere on the board

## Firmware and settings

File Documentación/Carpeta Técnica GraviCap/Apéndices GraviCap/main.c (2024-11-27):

#include <stdio.h>
#include <string.h>
#include "pico/stdlib.h"
#include "pico/binary_info.h"
#include "hardware/i2c.h"
#include "hardware/pwm.h"
#include "hardware/adc.h"
#include "hardware/irq.h"

#define PWM_WRAP                        3787  // Definimos frecuencia del micro, sin prescaler, 33kHz
#define ADC_GPIO_BATTERY                26
#define ADC_IN                          27
#define ADC_CURRENT_BATTERY             28
#define ADC_CHANNEL_BATTERY             0
#define ADC_CHANNEL_IN                  1
#define ADC_CURRENT_CHANNEL_BATTERY     2

#define BATTERY_ADC_RATIO               5.5     // Habra un ratio de 5 a 1 en el voltaje leido por el ADC y la bat
#define BATTERY_IN_RATIO                14.8    

#define BULK_MAX_BATTERY_VOLTAGE        26.5
#define BULK_MAX_CURRENT_VOLTAGE        4

#define ABSORTION_MAX_BATTERY_VOLTAGE   26.5   // Umbral de tension del modo ABSORTION
#define ABSORTION_MAX_PANEL_CURRENT     4
#define ABSORTION_MIN_PANEL_CURRENT     0.2

#define FLOAT_MAX_BATTERY_VOLTAGE       25.5
#define FLOAT_MIN_BATTERY_VOLTAGE       24
#define FLOAT_MAX_CURRENT_VOLTAGE       0.6
 
#define BATTERY_MIN_VOLTAGE             23.5     

#define INTEGRAL_CONSTANT               3  

#define MAX_LINES      4
#define MAX_CHARS      20

#define PICO_DEFAULT_I2C_SDA_PIN    4
#define PICO_DEFAULT_I2C_SCL_PIN    5

float prom_minute = 0;
float prom_hour = 0;
float real_prom = 0;
int cont_minute = 0; 
int cont_hour = 0;

float battery_in = 0;
float battery_voltage = 0;
float battery_current = 0;

typedef enum {
    BULK_MODE,
    ABSORTION_MODE,
    FLOAT_MODE,
    SPIKE_MODE
} charging_mode_t;

inline static uint16_t saturador(uint16_t wrap, int16_t level);
int64_t alarm_callback(alarm_id_t id, void *user_data);
float med_volt();
float med_current();
float med_in();

int main() {
    stdio_init_all();

    sleep_ms(3000);

    i2c_init(i2c_default, 100 * 1000);
    gpio_set_function(PICO_DEFAULT_I2C_SDA_PIN, GPIO_FUNC_I2C);
    gpio_set_function(PICO_DEFAULT_I2C_SCL_PIN, GPIO_FUNC_I2C);
    gpio_pull_up(PICO_DEFAULT_I2C_SDA_PIN);
    gpio_pull_up(PICO_DEFAULT_I2C_SCL_PIN);

    bi_decl(bi_2pins_with_func(PICO_DEFAULT_I2C_SDA_PIN, PICO_DEFAULT_I2C_SCL_PIN, GPIO_FUNC_I2C));
    
    uint8_t pwm = 15;
    uint8_t slice = pwm_gpio_to_slice_num(pwm);
    int16_t pwm_level = PWM_WRAP / 2;

    // Se define el modo inicial como BULK
    charging_mode_t charging_mode = BULK_MODE;

    // Inicializacion del ADC
    adc_init();
    adc_gpio_init(ADC_GPIO_BATTERY);
    adc_gpio_init(ADC_CURRENT_BATTERY);
    adc_select_input(ADC_CHANNEL_BATTERY);

    // Habilito GPIO como salida de PWM
    gpio_set_function(pwm, GPIO_FUNC_PWM);

    // Wrap para 33 KHz de PWM a 125 MHz de clock
    pwm_set_wrap(slice, PWM_WRAP);

    // 50% de ancho de pulso de partida
    pwm_set_gpio_level(pwm, pwm_level);

    // Habilitar PWM
    pwm_set_enabled(slice, true);

    add_alarm_in_ms(-1000, alarm_callback, NULL, false);

    while (true) {
        // Selecciono el canal de la tension y se lee y se convierte
        adc_select_input(ADC_CHANNEL_BATTERY);
        battery_voltage = med_volt();

        // Selecciono el canal de la corriente y se lee y se convierte
        adc_select_input(ADC_CURRENT_CHANNEL_BATTERY);
        battery_current = med_current();

        // Selecciono el canal de la entrada de tension, se lee y se convierte
        adc_select_input(ADC_CHANNEL_IN);
        battery_in = med_in();

        if (charging_mode == BULK_MODE){
            if (battery_voltage > BULK_MAX_BATTERY_VOLTAGE) {
                    // Cambio modo de carga en caso de que corriente baje del umbral
                    charging_mode = ABSORTION_MODE;
                }
            else {
                printf("BULK\n");
            }
        }
        if (charging_mode == ABSORTION_MODE){
            if (battery_current < ABSORTION_MIN_PANEL_CURRENT) {
                    // Cambio modo de carga en caso de que corriente baje del umbral
                    charging_mode = FLOAT_MODE;
                }
            else{
                printf("ABSORTION\n");
            }
        }
        if (charging_mode == FLOAT_MODE){
            if (battery_voltage < FLOAT_MIN_BATTERY_VOLTAGE) {
                    charging_mode = BULK_MODE;
                }  
            if (battery_current > FLOAT_MAX_CURRENT_VOLTAGE) {
                    // Cambio modo de carga en caso de que corriente exceda umbral
                    charging_mode = BULK_MODE;
                }
            else{
                printf("FLOAT\n");
            }
        }
    ///////////////   END MDOE VERIFICATION   ///////////////   
    
    ///////////////   BULK   ///////////////
        if (charging_mode == BULK_MODE) {
            float error = (BULK_MAX_CURRENT_VOLTAGE - battery_current) * 25;
            if (battery_current > BULK_MAX_CURRENT_VOLTAGE) {
                pwm_level = pwm_level - (-1 * error * INTEGRAL_CONSTANT);
            }
            else {
                pwm_level += 1 * error * INTEGRAL_CONSTANT;
            }
            // Verifico que no exceda los limites
            pwm_level = saturador(PWM_WRAP, pwm_level);
            // Ajusto PWM
            pwm_set_gpio_level(pwm, pwm_level);
        }
    ///////////////   END BULK   ///////////////
    
    ///////////////   ABSORTION   ///////////////
        if (charging_mode == ABSORTION_MODE)  {
            float errorv = (ABSORTION_MAX_BATTERY_VOLTAGE - battery_voltage) * 6.849315;
            float errorc = (ABSORTION_MAX_PANEL_CURRENT - battery_current) * 25;
            if(battery_current > ABSORTION_MAX_PANEL_CURRENT) {
                pwm_level = pwm_level - (-1 * errorc * INTEGRAL_CONSTANT);
            }  
            else if(battery_voltage > ABSORTION_MAX_BATTERY_VOLTAGE) {
                // Incremento el duty en una unidad
                pwm_level += 1 * errorv * INTEGRAL_CONSTANT;
            }
            else {
                pwm_level = pwm_level - (-1 * errorv * INTEGRAL_CONSTANT);
            }
            // Verifico que no exceda los limites
            pwm_level = saturador(PWM_WRAP, pwm_level);
            // Ajusto PWM
            pwm_set_gpio_level(pwm, pwm_level);
        }
    ///////////////  END ABSORTION  ////////////////

    ///////////////  FLOAT  ////////////////
        if(charging_mode == FLOAT_MODE) {
            float error = (FLOAT_MAX_BATTERY_VOLTAGE - battery_voltage) * 7.24638;
            if (battery_voltage > FLOAT_MAX_BATTERY_VOLTAGE){
                pwm_level = pwm_level - (-1 * error * INTEGRAL_CONSTANT);
            }
            else {
                pwm_level += 1 * error * INTEGRAL_CONSTANT;
            }
            // Verifico que no exceda los limites
            pwm_level = saturador(PWM_WRAP, pwm_level);
            // Ajusto PWM
            pwm_set_gpio_level(pwm, pwm_level);
        }
    ///////////////  END FLOAT  ////////////////
        printf("final, %f\n", pwm_level * 0.0264061262);
    }
    return 0;
}



// Saturador basico, se asegura que el PWM no sea ni negativo ni que se exceda del wrap
inline static uint16_t saturador(uint16_t wrap, int16_t level) {
    if(level > PWM_WRAP) {
        level = PWM_WRAP;
        return PWM_WRAP;
    }
    else if(level < 0) {
        level = 0;
        return 0;
    }
    return level;
}

int64_t alarm_callback(alarm_id_t id, void *user_data) {
    if(cont_minute < 60){
        prom_minute += (battery_in * battery_current);
        cont_minute += 1;
    }
    else{
        prom_hour += (prom_minute / cont_minute);
        cont_hour += 1;
        cont_minute = 0;
    }
    return 0;
}

float med_volt(){
    float prom = 0;
    for (int i = 0; i < 10; i++){
        float volt = BATTERY_ADC_RATIO * adc_read() * 3.3 / (1 << 12);
        prom = prom + volt;
        }
    return prom/10;
}

float med_current(){
    float prom = 0;
    for (int i = 0; i < 10; i++){
        float current = ((adc_read() * 3.3 / (1 << 12)) - 2.565) * (-10);
        prom = prom + current;
    }
    return prom/10;
}

float med_in(){
    float prom = 0;
    for (int i = 0; i < 10; i++){
        float volt = BATTERY_IN_RATIO * adc_read() * 3.3 / (1 << 12);
        prom = prom + volt;
    }
    if (prom < 5){
        prom = 0;
    }
    return prom/10;
}

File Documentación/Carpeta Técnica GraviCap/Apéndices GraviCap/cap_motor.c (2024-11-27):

#include "cap_motor.h"

// Variables para las mediciones particulares de cada sensor
extern mediciones_ina219 m_ina0x40;
extern mediciones_ina219 m_ina0x41;
extern mediciones_ina219 m_ina0x44;
extern mediciones_ina219 m_ina0x45;

extern queue_t queue_core_1_motor;

extern float carga, last_carga_motor;

int down = 0;

void carga_motor(int rele_carga) {
  down = 0;
  gpio_put(RELE_DESCARGA, 0);
  gpio_put(RELE_STOP, 1);
  gpio_put(RELE_CARGA, 1);

  gpio_put(LED_STOP, 1);
  gpio_put(LED_DESCARGA, 0);
  gpio_put(LED_CARGA, 0);
  return;
}

int descarga_motor() {
  if (down == 0) {
    // Cuando llamo a descargar el motor

    // Configuro relés y leds para el estado de descarga
    gpio_put(RELE_STOP, 1);
    gpio_put(RELE_CARGA, 0);
    gpio_put(RELE_DESCARGA, 1);
    
    gpio_put(LED_STOP, 0);
    gpio_put(LED_DESCARGA, 1);
    gpio_put(LED_CARGA, 0);

      // Trato de recoger los datos de una queue con los datos
      // la última carga del motor y la más reciente
    if (queue_try_peek(&queue_core_1_motor, &carga)) {
      queue_remove_blocking (&queue_core_1_motor, &carga);
      last_carga_motor = carga;
    }
    else {
      // FALLAS EN EL ENCODER, NO ESTÁ MANDANDO DATOS
      printf("POSIBLE FALLA EN EL ENCODER NO HAY TRANSFERENCIA DE DATOS\n");
      return 2;
    }

    gpio_put(RELE_DESCARGA, 0);
    // YA RECIBIÓ SU PRIMER VALOR DE CARGA
    // Y DIO UN PULSO DE DESCARGA
    down = 1;
    return 0; // lleva a un delay
  }
  else if (down == 1) {
    if (queue_try_peek(&queue_core_1_motor, &carga)) {
      queue_remove_blocking(&queue_core_1_motor, &carga);
    }
    else {
      printf("POSIBLE FALLA EN EL ENCODER NO HAY TRANSFERENCIA DE DATOS\n");
      return 2;
    }
    
    // YA TRATÓ DE DESCARGAR UNA VEZ SIN PASAR POR UNA CARGA O STOP
    if (last_carga_motor == carga) {
      // No está descargando
      gpio_put(RELE_DESCARGA, 1);
      gpio_put(RELE_DESCARGA, 0);
      return 1; // delay
    }
    else {
      // debería estar descargando, lo llevo a un delay
      return 1; // delay
    }

  }
  else {
    return 1;
  }
}

// Función para frenar el motor
void motor_stop() {
  down = 0;
  gpio_put(RELE_DESCARGA, 0);
  gpio_put(RELE_DESCARGA, 0);
  gpio_put(RELE_STOP, 0); // Al ser un normal cerrado, se mantiene cerrado en 0, está puenteado
  
  gpio_put(LED_STOP, 1);
  gpio_put(LED_DESCARGA, 0);
  gpio_put(LED_CARGA, 0);

  printf("MOTOR EN PAUSA\n");
  return;
}

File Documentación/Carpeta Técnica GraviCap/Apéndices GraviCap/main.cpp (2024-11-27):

#include <ESP8266WiFi.h>
#include "ESPAsyncWebServer.h"
#include <Arduino.h>
#include <ArduinoJson.h>

bool pruebaEnviada = 0;

struct lectura {
  float carga;
  String nombre;
  float corriente;
  float voltage;
  float potencia;
};

lectura sensor_0x40;
lectura sensor_0x41;
lectura sensor_0x44;
lectura sensor_0x45;

const char* ssid = "Cooperadora Alumnos";
const char* password = "";

AsyncWebServer server(80);

void addCORSHeaders(AsyncWebServerResponse* response) {
  response->addHeader("Access-Control-Allow-Origin", "*");
  response->addHeader("Access-Control-Allow-Methods", "GET, POST, OPTIONS");
  response->addHeader("Access-Control-Allow-Headers", "Content-Type, X-Custom-Header");
}

void handleCORS(AsyncWebServerRequest *request) {
  AsyncWebServerResponse* response = request->beginResponse(200);
  addCORSHeaders(response);
  request->send(response);
}

void procesarJson(String json) {
  StaticJsonDocument<256> doc; // JsonDocument específico para tamaño estático
  DeserializationError error = deserializeJson(doc, json);
  if (error) {
    Serial.println("Error al parsear JSON:");
    Serial.println(error.c_str());
    return;
  }

  String nombre = doc["nombre"];  // Ahora se usa el campo "nombre" del JSON
  lectura* sensor = nullptr;

  // Compara el nombre para determinar a qué sensor se refiere
  if (nombre == "Sensor_0x40") {
    sensor = &sensor_0x40;
  } else if (nombre == "Sensor_0x41") {
    sensor = &sensor_0x41;
  } else if (nombre == "Sensor_0x44") {
    sensor = &sensor_0x44;
  } else if (nombre == "Sensor_0x45") {
    sensor = &sensor_0x45;
  }

  if (sensor) {
    sensor->carga = doc["carga"];
    sensor->nombre = nombre;
    sensor->corriente = doc["corriente"];
    sensor->voltage = doc["voltage"];
    sensor->potencia = doc["potencia"];
  } else {
    Serial.println("Sensor no reconocido: " + nombre);
  }
}

String generarRespuestaJson(lectura sensor) {
  StaticJsonDocument<256> doc; // JsonDocument estático
  doc["carga"] = sensor.carga;
  doc["nombre"] = sensor.nombre;
  doc["corriente"] = sensor.corriente;
  doc["voltage"] = sensor.voltage;
  doc["potencia"] = sensor.potencia;

  String response;
  serializeJson(doc, response);
  return response;
}

void setup_servidor() {
  server.on("/", HTTP_OPTIONS, handleCORS);
  server.on("/sensor", HTTP_OPTIONS, handleCORS);
  //server.on("/todos", HTTP_OPTIONS, handleCORS);

  server.on("/sensor", HTTP_GET, [](AsyncWebServerRequest *request) {
    if (!request->hasParam("nombre")) {
      AsyncWebServerResponse* response = request->beginResponse(400, "text/plain", "Falta el parámetro 'nombre'.");
      addCORSHeaders(response);
      request->send(response);
      return;
    }

    String sensorNombre = request->getParam("nombre")->value();
    String responseJson;

    // Compara el nombre recibido en la solicitud para determinar el sensor
    if (sensorNombre == "Sensor_0x40") {
      responseJson = generarRespuestaJson(sensor_0x40);
    } else if (sensorNombre == "Sensor_0x41") {
      responseJson = generarRespuestaJson(sensor_0x41);
    } else if (sensorNombre == "Sensor_0x44") {
      responseJson = generarRespuestaJson(sensor_0x44);
    } else if (sensorNombre == "Sensor_0x45") {
      responseJson = generarRespuestaJson(sensor_0x45);
    }

    else {
      Serial.println("Error: Sensor no encontrado");
      AsyncWebServerResponse* response = request->beginResponse(404, "text/plain", "Sensor no encontrado.");
      addCORSHeaders(response);
      request->send(response);
      return;
    }

    AsyncWebServerResponse* response = request->beginResponse(200, "application/json", responseJson);
    addCORSHeaders(response);
    request->send(response);
  });
  server.begin();
}

void setup() {
  Serial.begin(115200);

  Serial.println("\nConectando a ");
  Serial.print("Setting AP (Access Point)…");
  WiFi.begin(ssid, password);

  while (WiFi.status() != WL_CONNECTED) {
    delay(500);
    Serial.print(".");
  }
  Serial.println("WiFi conectado");
  Serial.println("Dirección IP: ");
  Serial.println(WiFi.localIP());

  Serial.println("\nServidor iniciado");
  setup_servidor();
}

void loop() {
  if (Serial.available()) {
    String json = Serial.readStringUntil('\n');
    Serial.println("Datos recibidos por UART:");
    Serial.println(json);
    procesarJson(json);
  }
  else if (!pruebaEnviada) {
    String json = "{\"nombre\":\"Sensor_0x40\",\"carga\":15.5,\"corriente\":2.3,\"voltage\":5.0,\"potencia\":11.5}";

    Serial.println("Prueba de JSON:");
    Serial.println(json);

    // Procesa el JSON de prueba
    procesarJson(json);

    // Cambia la bandera a true para evitar que se vuelva a enviar
    pruebaEnviada = true;
  }
}

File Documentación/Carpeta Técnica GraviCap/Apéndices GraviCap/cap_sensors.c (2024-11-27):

#include "cap_sensors.h"

// Variables para las mediciones particulares de cada sensor
extern mediciones_ina219 m_ina0x40;
extern mediciones_ina219 m_ina0x41;
extern mediciones_ina219 m_ina0x44;
extern mediciones_ina219 m_ina0x45;

// Registro de cada sensor
extern ina219_t ina219_0x40; // Consumo
extern ina219_t ina219_0x41; // Entrega del mppt
extern ina219_t ina219_0x44; // Consumo de la batería
extern ina219_t ina219_0x45; // Entrega del panel solar

extern QueueHandle_t queue_ina219_consulta_all;
extern QueueHandle_t queue_ina219_send_uart;

void task_lectura_sensor_ina219_0x40(void *params) {
  while(1){
    bool sent_40_all = false, sent_40_uart = false;
    printf("Lectura sensor INA219_0X40");
    m_ina0x40.ina = &ina219_0x40;
    m_ina0x40.corriente = ina219_read_current(ina219_0x40);
    m_ina0x40.voltage = ina219_read_voltage(ina219_0x40);
    m_ina0x40.power = ina219_read_power(ina219_0x40);

    if (sent_40_all == false) { 
      xQueueSend(queue_ina219_consulta_all, &m_ina0x40, pdMS_TO_TICKS(1000));
      sent_40_all = true;
    }
    if (sent_40_uart == false) { 
      xQueueSend(queue_ina219_send_uart, &m_ina0x40, pdMS_TO_TICKS(1000));
      sent_40_uart = true;
    }
    vTaskDelay(1000);
  }
}

void task_lectura_sensor_ina219_0x41(void *params) {
  while(1) {
    bool sent_41_all = false, sent_41_uart = false;
    printf("Lectura sensor INA219_0X41");
    m_ina0x41.ina = &ina219_0x41;
    m_ina0x41.corriente = ina219_read_current(ina219_0x41);
    m_ina0x41.voltage = ina219_read_voltage(ina219_0x41);
    m_ina0x41.power = ina219_read_power(ina219_0x41);

    if (sent_41_all == false) { 
      xQueueSend(queue_ina219_consulta_all, &m_ina0x41, pdMS_TO_TICKS(1000));
      sent_41_all = true;
    }
    if (sent_41_uart == false) { 
      xQueueSend(queue_ina219_send_uart, &m_ina0x41, pdMS_TO_TICKS(1000));
      sent_41_uart = true;
    }
    vTaskDelay(1000);
  }
}

void task_lectura_sensor_ina219_0x44(void *params) {
  while(1) {
    bool sent_44 = false;
    printf("Lectura sensor INA219_0X44");
    m_ina0x44.ina = &ina219_0x44;
    m_ina0x44.corriente = ina219_read_current(ina219_0x44);
    m_ina0x44.voltage = ina219_read_voltage(ina219_0x44);
    m_ina0x44.power = ina219_read_power(ina219_0x44);

    if (sent_44 == false) {
      xQueueSend(queue_ina219_send_uart, &m_ina0x44, pdMS_TO_TICKS(1000));
      sent_44 = true;
    }
    vTaskDelay(1000);
  }
}

void task_lectura_sensor_ina219_0x45(void *params) {
  while(1) {
    bool sent_45 = false;
    printf("Lectura sensor INA219_0X45");
    m_ina0x45.ina = &ina219_0x45;
    m_ina0x45.corriente = ina219_read_current(ina219_0x45);
    m_ina0x45.voltage = ina219_read_voltage(ina219_0x45);
    m_ina0x45.power = ina219_read_power(ina219_0x45);

    if (sent_45 == false) {
      xQueueSend(queue_ina219_send_uart, &m_ina0x45, pdMS_TO_TICKS(1000));
      sent_45 = true;
    }
    vTaskDelay(1000);
  }
}

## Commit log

2024-08-26 feat: Configuracion para build en github pages
2024-08-26 feat: Instalado la extensión de github pages
2024-08-26 feat: homepage de config
2024-08-26 chore:"cambiando base para el github pages 2"
2024-08-30 Add File "Esquemático - MPPT" & "PCB - MPPT"
2024-08-30 Create "PCB"
2024-08-30 Add Files "Esquemático - MPPT" & "PCB - MPPT"
2024-09-02 add: "Archivos de etapa de control"
2024-10-02 feat: Subo la aplicación
2024-10-02 feat: uso de multicore en la etapa de control
2024-10-11 perf: funcion que envía datos a la esp
2024-10-14 refactor: función de status
2024-10-15 fix: posibles bugs & correct: nombres de variables
2024-10-15 add: encendido de leds de estado y cargador
2024-10-15 fix: orden de tareas de FreeRTOS
    [main.c]
2024-10-18 fix: funciones de carga, descarga y stop del motor
2024-10-18 fix: errores de la función de descarga
2024-10-28 feat: Añadí los archivos de LaTeX
2024-10-28 feat: Creación de una carpeta de Imagenes.
2024-10-28 fix: "Error en la imágen"
2024-10-28 fix: "Error en la Imagen v2"
2024-10-28 fix: "Error en la Tabla"
2024-10-28 fix: "Error en la Tabla v2"
2024-10-31 feat: "cambiar imágenes de la página web con las de la ONIET"
2024-10-31 feat: "Añadí archivos de los PCB de Etapa de Control y del Step-Down"
    [Etapa_de_Control.kicad_pcb, Etapa_de_Control.kicad_sch, Placa de Conexión..kicad_pcb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]
2024-10-31 fix: "Archivos Equivocados"
    [Placa de Conexión..kicad_pcb, Placa de Conexión..kicad_sch]
2024-11-03 fix: "Corrección de errores de la placa"
    [estapa_de_control.kicad_pcb]
2024-11-03 feat: "Se añaden los archivos de la placa de la Etapa de Control"
    [estapa_de_control.kicad_pcb, estapa_de_control.kicad_sch]
2024-11-03 fix: "Archivos Incorrectos"
    [estapa_de_control.kicad_pcb, estapa_de_control.kicad_sch]
2024-11-03 feat: "Se añade un Readme para la Placa de Conexión"
2024-11-03 feat: "Archivos del PCB de la Etapa de Control"
    [estapa_de_control.kicad_pcb, estapa_de_control.kicad_sch]
2024-11-03 feat: "Nuevos archivos"
    [estapa_de_control.kicad_pcb, estapa_de_control.kicad_sch]
2024-11-05 feat: Modelo Estructura a Escala
    [Gravicap v3 a escala v1.f3d]
2024-11-05 Feat: Archivos de Diseño de Estructura
    [Gravicap v3 a escala v1.f3d, ejemplo de elevación.stl]
2024-11-05 build: reorganización de los archivos de la librería
2024-11-05 feat: "Añadí versión 2 de la Carpeta Ténica"
2024-11-05 feat: "Eliminación de la versión 1 de la Carpeta Ténica"
2024-11-05 feat: "Añado los Apéndices de la Carpeta Ténica"
2024-11-05 build: reorganización de los archivos de librería SENSORES
2024-11-05 fix: función de descarga del motor
2024-11-05 style: correcciones según convenciones de estilo en C
2024-11-08 docs: Subo mockup de la app
2024-11-09 feat: modifico el color de las letras del botón
2024-11-09 fix: configuración pull up en los leds
    [main.c]
2024-11-09 feat: añado texto en la pantalla de bienvenida
2024-11-09 feat: modifico posiciones de texto y botón
2024-11-10 feat: Cambios en los archivos para poder usar Android Studio
2024-11-10 feat: "Creación de Carpeta para la presentación del video y añado archivos"
2024-11-10 feat: "Añado archivos de audio"
2024-11-11 feat: "Subo audio de la Aplicación Móvil"
2024-11-11 feat: audio de agradecimientos
2024-11-11 feat: audio etapa de control
2024-11-11 feat: "Añado archivos de audio de Augusto"
2024-11-15 feat: agrego cors y cambio de puerto
2024-11-16 feat: primera muestra de datos con el server
2024-11-16 feat: cambio total de la lógica, funciona
2024-11-18 feat: "Correcciones realizadas a la placa"
    [GraviCap.kicad_pcb, GraviCap.kicad_sch]
2024-11-20 fix: ahora sí funciona
    [main.c]
2024-11-20 style: cambio de nombre según convenciones utilizadas
2024-11-20 style: limpieza del código y correcciones según convenciones de c
2024-11-21 docs: subo carpeta para los apks de la app
2024-11-21 feat: "Creación del readme.md para Documentación"
2024-11-21 feat: se cambió el logotipo de la app en android sudio
2024-11-21 feat: se modificaron los tamaños y posiciones de los componentes de la app
2024-11-21 feat: "Archivos .pdf de la Documentación (Final)"
2024-11-21 feat: "Manual de Usuario (Final)"
2024-11-21 fix: "Error de Escritura"
2024-11-21 feat: "Creación de Carpeta Imágenes"
2024-11-21 feat: link de app móvil en readme
2024-11-21 feat: "Código Manual de Usuario (Final)"
2024-11-21 feat: imágenes de la placa de la etapa de control
2024-11-21 feat: prueba exitosa de muestra de datos en tiempo real
2024-11-25 fix: mini arreglos diversos para que funcione (1)
    [main.c]
2024-11-25 chore: imagen del diagrama de tareas
2024-11-25 chore: imagen del diagrama de tareas .png
2024-11-25 chore: diagrama de tareas de freertos
2024-11-25 subo versiones de la app
2024-11-25 muestra de datos a tiempo real en las pantallas
2024-11-25 limpieza y comentación de código
2024-11-25 fix: actualización de versión de archivo de android studio
2024-11-26 feat: valor de potencai en inicio y ajusto su tamaño
2024-11-26 fix: mini arreglos diversos para que funcione (2)
    [main.c]
2024-11-27 chore: facturas de compras
2024-11-27 fix: coloco bien el Readme
2024-11-27 chore: agrego factura de compra de cable
2024-11-27 chore: diagramas para presentación final
2024-11-27 chore: Añado las Facturas de Compras
2024-11-28 feat: nuevas versiones finales para la aplicación
2024-11-28 feat: subo diagramas de flujo
2024-11-29 chore: "Se arregla la descripción acorde a lo subido recientemente"
2024-11-30 feat: "Añado la Presentación"
